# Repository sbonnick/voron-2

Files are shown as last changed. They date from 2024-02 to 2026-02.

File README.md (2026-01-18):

# voron-2

this repository contains everything you need image, update and operate a voron 2.4r2 3D printer. There are several mods used on my current voron 2.4r2 setup. These mods will be made clear if they require code or system level changes. If you do not have specific mods I will attempt to make it clear what alternative configurations are needed when possible. 

## Roadmap

This repo and doc is still missing some critical items to be fully up and running. some of these items that need to be dome before that milestone is reached are:

TODO:
- [ ] rewire octopus to use usb or CAN
- [ ] identify the configuration items that need to be adjusted
- [ ] script binary creation. use docker
- [ ] more details for the first init setup
- [ ] need to add knomi v2
- [ ] need to add chamber sensor
- [ ] consider adding a heat up (120c) and clean of nozzle before the z calibration
- [ ] create docker for katapult
- [ ] fully automate upgrading binaries

## Component Variants and Mods

| Description | Hardware Variants | Mods | Software Impacts |
| ---|---|---|---|
| Linux PCB | Pi4 2G - piOS | heat sync | Major |
| Main MCU PCB | BTT Octopus Pro | | Major |
| Toolhead PCB | BTT EBB 2240 CAN | [motor mount, cable chain arm](https://github.com/bigtreetech/EBB/tree/master/EBB%20SB2240_2209%20CAN/STL), [cable cover](https://www.printables.com/model/1216990-stealthburner-cable-cover-for-sb2209-rp2040) | Major |
| USB to CAN | BTT U2C | [mount](https://mods.vorondesign.com/detail/guUSuCXHsOqPH1Xn5cS1Ag) | Major |
| Extruder Motor | LDO-36STH20 | | |
| Z Motors | LDO-42STH48 | | Minor |
| A/B Motors | LDO-42STH40 | [plug mounts](https://github.com/Ramalama2/Voron-2-Mods/tree/main/AB_Plugs), [cable clips](https://github.com/Ramalama2/Voron-2-Mods/tree/main/Misumi_Cable_Clip) | Minor |
| Hotend | Voron Dragon HF | | |
| Extrusion support | Titanium Extrusion Backers | | |
| Kinematic Bed |  | [kinematic parts](https://github.com/tanaes/whopping_Voron_mods/tree/main/kinematic_bed) | |
| Hotend cleaning | nozzle scrubber | [brush wiper](https://www.printables.com/model/768112-voron-24-a1-bambu-silicone-brush-wiper), [brush mount](https://www.printables.com/model/659369-voron-24-purge-bucket-silicon-brush-wiper), [Purge Bucket for Kinematic](https://github.com/Dfdye/Voron_Mods/tree/main/Purge_Bucket_for_WP_Kinetic_Mount) | Minor |
| Run out sensor | BTT SFS v2.0 Sensor | [mount](https://www.printables.com/model/713155-bigtreetech-smart-filament-sensor-sfs-v20-2020-ext) | Minor |
| Exhaust | ? | ? | Minor |
| Air Filter | Nevermore 5 v2 | [parts](https://github.com/nevermore3d/Nevermore_Micro/tree/master/V5_Duo/V2) | Minor |
| X/Y End stops | Mellow Hall PCB | | Minor |
| Probe / Z end stop | CNC Voron Tap v2 | [hall sensor mount](https://github.com/Chaoticlab/CNC-Tap-for-Voron/blob/master/STL/CNC_VORON_TAP_V2/V2%20Hall%20Sensor%20Adapter.STL) | Major |
| Misc. wiring mods |  | [rails](https://mods.vorondesign.com/detail/ozerX2agbmmnjUP4EdDyQ), [under bed wagos](https://mods.vorondesign.com/detail/Zdq86RuSkhr4bx3xrauw) | |
| Misc. case mods |  | [hinges](https://mods.vorondesign.com/detail/eeRCH8EJiLrIF5q5l3AQg), [lean supports](https://mods.vorondesign.com/detail/tiIhFDTh9tHJY0JNJK9A), [handles](https://mods.vorondesign.com/detail/EAM1ZiQJCUzXznvOA767w), [magnets mount top](https://www.teamfdm.com/files/file/324-magnetic-panels/), [bottom panel tabs](https://www.teamfdm.com/files/file/134-deck-panel-support-clips/) | |
| Lights | | [mount segment](https://mods.vorondesign.com/detail/8S6KN4daUCgRhEJEX1stQ), [mount ends](https://github.com/Ramalama2/Voron-2-Mods/tree/main/Deprecated/Misumi_Led_Corners/STL), [idler corners](https://mods.vorondesign.com/detail/zBJTvWc9vSnnQoDDP0hyYw), [z corner covers](https://www.printables.com/model/84736-z-belt-cover-a-for-voron-24) | |
| power supply mods |  | [double din mount](https://www.teamfdm.com/files/file/457-double-din-lrs200-24-mounts-for-voron-24/), [terminal cover](https://mods.vorondesign.com/detail/jyO8bHoPTy3XUaYlXscB7w) | |
| Thermistor | PT100 | | Minor |
| Web Camera | Logitech C920s | [Top Mount](https://mods.vorondesign.com/detail/XgriEYTt4Xl5LeDx5DnPRg) | Major |
| Umbilical clamps | Canbus | [Clamps](https://makerworld.com/en/models/142656-voron-cable-clamp-umbilical-mod-canbus#profileId-180684) | Minor |

All mods are also stored in the stl folder for version locking. As I upgrade versions these will be upgraded as well based on the original authors revisions.

## Wiring

| Description | Images |
|---|---|
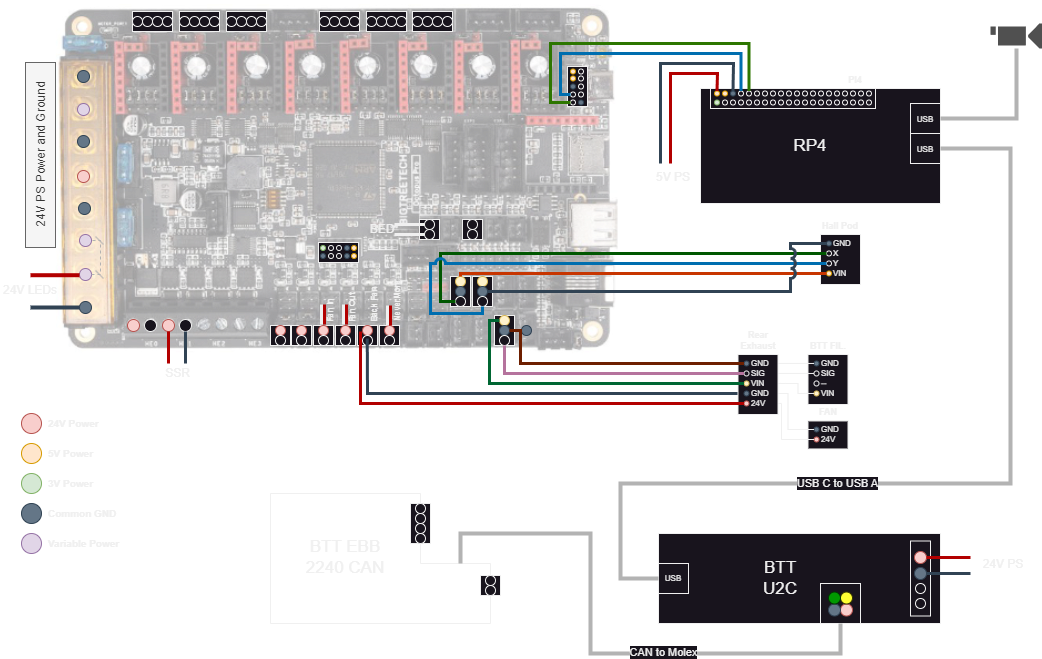
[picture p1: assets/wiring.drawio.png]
wiring diagram
| Overall wiring diagram |  |
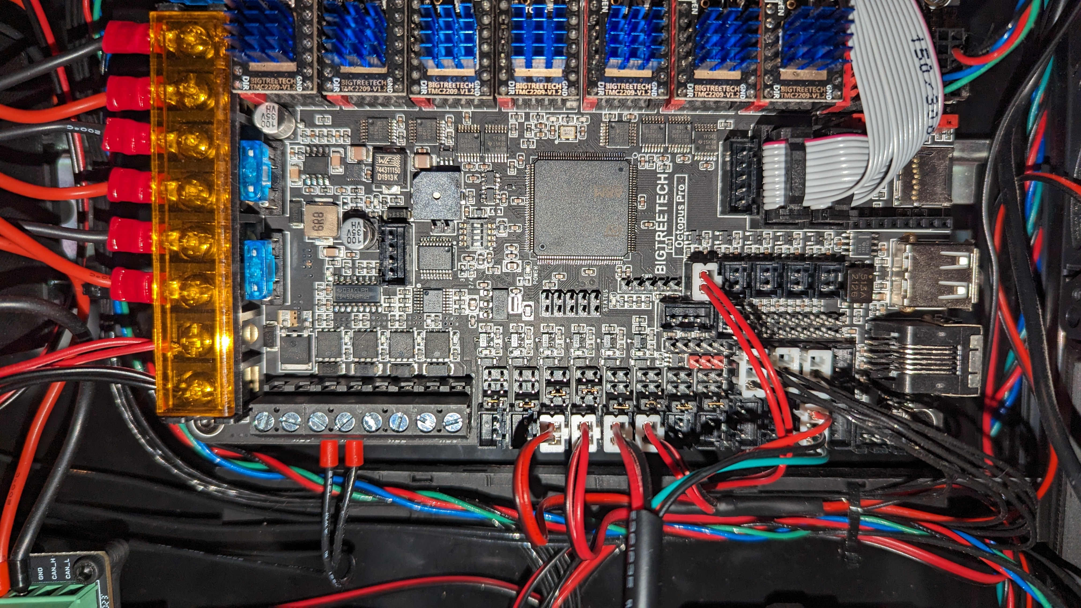
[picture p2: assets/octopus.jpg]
octopus
| Wiring for the Octopus. Note that currently the Octopus is using serial to communicate with the pi4. a future iteration I plan to switch back to usb connection or CAN |  |
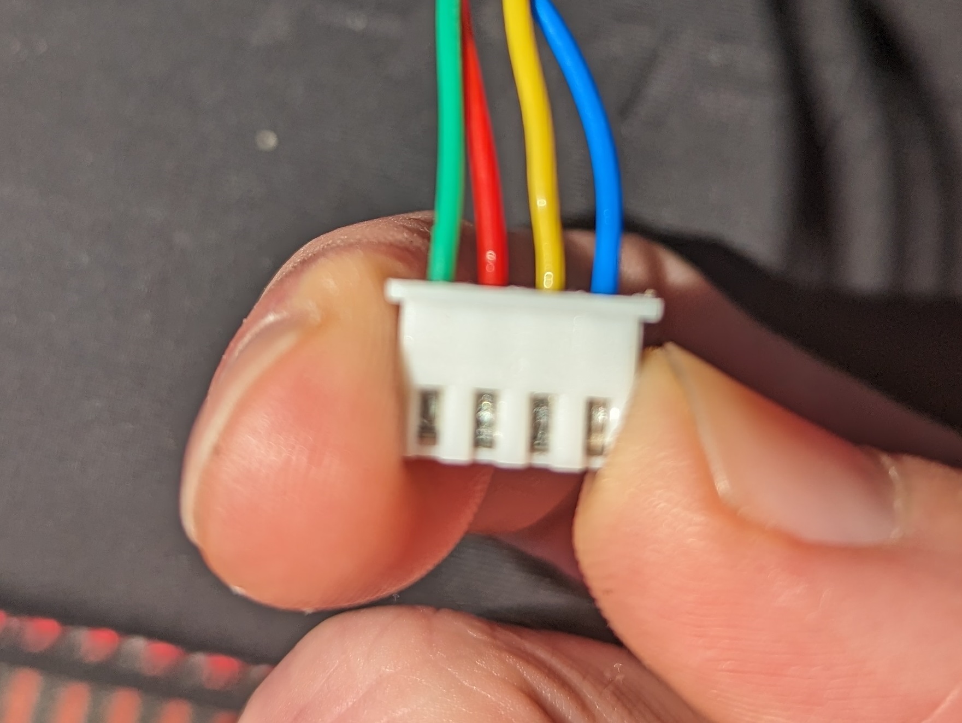
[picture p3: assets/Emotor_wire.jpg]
Extruder motor wiring
| When shortening the extruder wire, it will also require reordering the pins. Here is the order if its the LDO 20mm motor. If you use a different motor ensure you have the ordering correct |  |
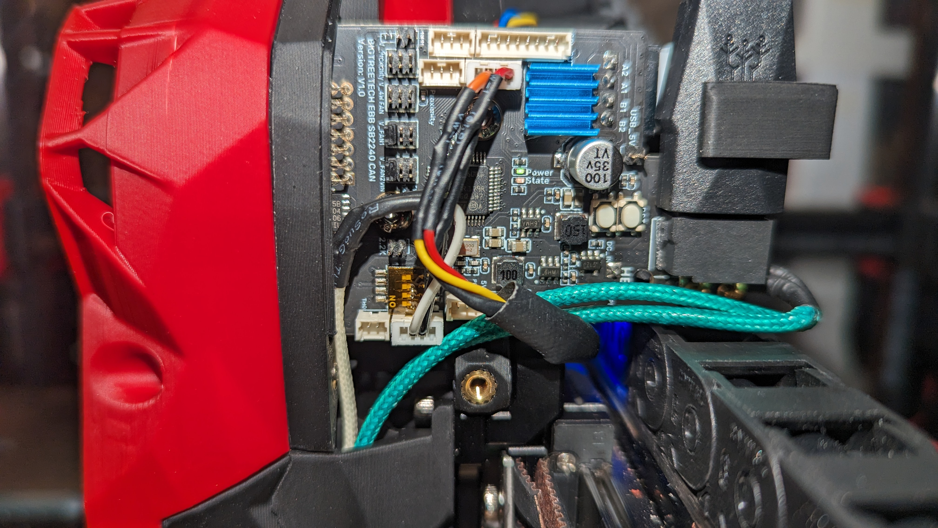
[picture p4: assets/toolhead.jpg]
Toolhead wiring
| Wiring for BTT EBB 2240 CAN Toolhead. Using PT100 (set the dip switches!) LDO motor wired above, and a voron TAP |  |
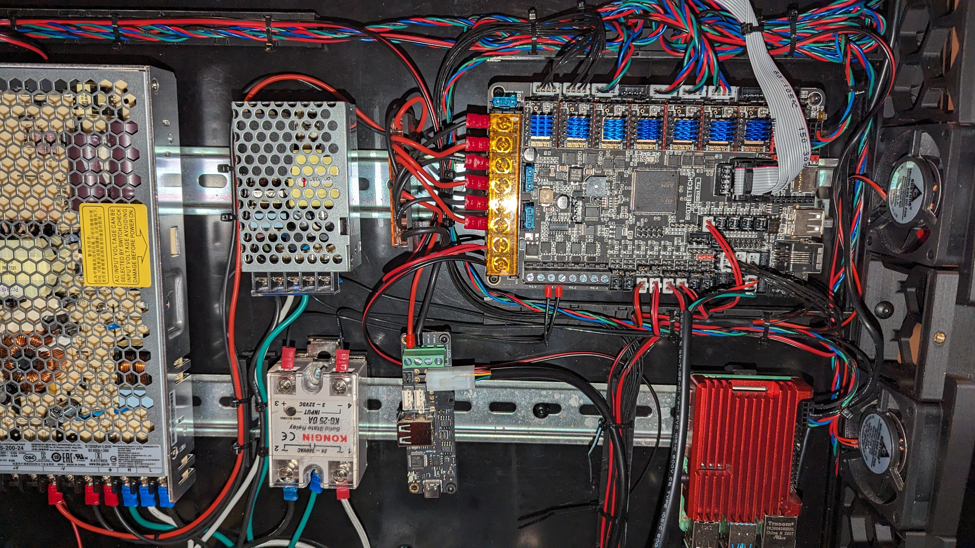
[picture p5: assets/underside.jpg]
underside
| Overall view of underside of voron 2 fully wired with all mods in place | |

## System Provisioning and Firmware

### Setup RaspberryPi 4 and Essential Software

Download the raspberry pi imaging tool and follow the steps to edit settings for an appropriate hostname, username, password, timezone, and ssh to format a micro sd card. Then install into the raspberry pi. Follow the rest of the steps over SSH.

Following SSH into the new machine, run the following:
```
sudo apt update
sudo apt upgrade -y
curl -sSL https://get.docker.com | sh
sudo usermod -aG docker $USER
sudo apt-get install gcc-arm-none-eabi dfu-util
```

### Setup UART

1. Disable bt
```
sudo nano /boot/firmware/config.txt
```
2. add the following
```
dtoverlay=disable-bt
```
3. remove `console=serial0,115200` from cmdLine.txt file
```
sudo nano /boot/firmware/cmdline.txt
```
4. reboot

### Setup U2C

1. Enter the following command to setup the CAN Network
```
sudo systemctl enable systemd-networkd
sudo systemctl start systemd-networkd
sudo systemctl disable systemd-networkd-wait-online.service
echo -e 'SUBSYSTEM=="net", ACTION=="change|add", KERNEL=="can*"  ATTR{tx_queue_len}="128"' | sudo tee /etc/udev/rules.d/10-can.rules > /dev/null
echo -e "[Match]\nName=can*\n\n[CAN]\nBitRate=1M\n\n[Link]\nRequiredForOnline=no" | sudo tee /etc/systemd/network/25-can.network > /dev/null
sudo reboot now

```
2. Install repos we know we will need to use
```
git clone https://github.com/Arksine/katapult.git
git clone https://github.com/sbonnick/voron-2.git

```
3. Setup docker stack
```
mkdir -p ~/core/klipper/log
mkdir -p ~/core/klipper/config
mkdir -p ~/core/klipper/moonraker-db
nano ~/core/.env
```
4. Add the following content to the .env
```
PUID=1000
PGID=1000
TZ="America/Toronto"
INSTALLDIR=/home/administrator/core
```
5. Copy specific files
```
cp ~/voron-2/docker-compose.* ~/core/
cp ~/voron-2/configs/klipper/* ~/core/klipper/config/
```
6. Modify docker compose file and klipper configs accordingly

### Setup Toolhead MCU

To reduce wiring complexity and portability, I have replaced my hardwired toolhead with BTTs EBB 2240 CAN board. If you are using a hard wired setup using something like a Hartk PCB, you can ignore these setup steps since your toolhead will not have a independent MCU. Caution though, your wiring will look very different as a result. refer to a older check-in here if you want to see my legacy Hartk PCB setup.

#### Building and Installing Katapult (Canboot) on EBB

1. Ensure 24V power and CAN lines are unplugged. Plug usb-c into the EBB 2240 and set the usb-c 5v power jumper
2. Run the following commands, or jump to the next step if using the prebuilt binary
```
cd katapult
make -f ../configs/toolhead.katapult.config
cd ..
```
3. Enter DFU mode on the toolhead by holding boot and clicking reset
4. Run `lsusb` and use the USB ID in the following command to flash the pre-built binary `~/voron-2/bin/toolhead.katapult.bin` or the one created in `~/katapult/out/katapult.bin`.
```
sudo dfu-util -a 0 -d 0483:df11 -s 0x08000000:mass-erase:force -D ~/CanBoot/out/canboot.bin
```
5. remove usb-c and 5v jumper. Hook back up the 24V power and CAN lines.

#### Building and Installing Klipper on EBB (fresh install or upgrade)

Before updating firmware, you need to ensure the same version of klipper is being used. Create a `.env` file and add the tag that is being used by the klipper app in docker. for example `TAG=v0.12.0-439-g1fc6d214f`. this can be retrieved using:
```
docker inspect --format '{{ index .Config.Labels "org.prind.image.version"}}' klipper
```

1. Run the following commands, or jump to the next step if using the prebuilt binary
```
cd ~/core
docker-compose -f docker-compose.toolhead.build.yml run --rm make
cp ./klipper/out/klipper.bin toolhead.klipper.bin
```
2. Run the following commands to get into katapult bootloader
```
python3 ~/katapult/scripts/flashtool.py -i can0 -r -u 8b07d889b7ef
python3 ~/katapult/scripts/flashtool.py -i can0 -q	# should show katapult app
```
If you don't already have your ID, then you need to double click the reset button (back button) on the toolhead to get into this mode. you can then run the query (-q) with same expectations. It will also provide your ID.

3. Flash the binary we create earlier
```
python3 ~/katapult/scripts/flashtool.py -i can0 -f ~/voron-2/bin/toolhead.klipper.bin -u 8b07d889b7ef
python3 ~/katapult/scripts/flashtool.py -i can0 -q	# should show klipper app
```
4. Cycle power

### Setup Octopus MCU

Before updating firmware, you need to ensure the same version of klipper is being used. Create a `.env` file and add the tag that is being used by the klipper app in docker. for example `TAG=v0.12.0-439-g1fc6d214f`. this can be retrieved using:
```
docker inspect --format '{{ index .Config.Labels "org.prind.image.version"}}' klipper
```

1. Run the following commands, or jump to the next step if using the prebuilt binary
```
cd ~/core
docker-compose -f docker-compose.octopus.build.yml run --rm make
cp ./klipper/out/klipper.bin octopus.klipper.bin
```
2. Use the samba share to copy the bin to a sd-card on your computer. rename the file `firmware.bin`.
3. Insert the sd-card into your octopus mcu and reboot (cycle power)
4. Wait 5 minutes, power down and remove sd-card. power back on
5. validate there is no longer a `firmware.bin` on the sd-card

## Klipper Configuration

TODO: list here any parameters that need to be adjusted from the `klipper.cfg` included.

## Initial Setup and Test

Once wiring and software are up and going, run through the tests and setup on:

- https://ellis3dp.com/Print-Tuning-Guide
- https://www.klipper3d.org/Config_checks.html

To calibrate dimensions of your printer use the follow pattern:

- [Calistar](https://thangs.com/designer/realdirtdigger/3d-model/Calistar%20%28formerly%20Fleur%20de%20Cali%29%20-%20Open%20source%20printer%20size%20and%20skew%20calibration-102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)

Anytime something changes that can effect the thermals of the printer, pid calibration is needed. changing sensors, hotends, etc would require this. The following command can be run in fluidd terminal and will output new pid values to be added into the printer.cfg. 
```
PID_CALIBRATE HEATER=extruder TARGET=260

or

PID_CALIBRATE HEATER=heater_bed TARGET=105
```

Anytime mechanical parts are changed, you need to redo the resonance testing:
```
SHAPER_CALIBRATE
```

## Slicing

TODO: add slicer specific settings and steps to do. OrcaSlicer configuration steps are a good one.

### Cura

Install cura from: https://ultimaker.com/software/ultimaker-cura/

If using Cura, install the following Plugins:
- Settings Guide
- Linear Advance Settings
- Mesh Tools
- Moonraker Connection
- Settings Exporter

Download the following script and install as per instructions:
- https://github.com/pedrolamas/klipper-preprocessor

Download latest processor.exe and put on C: path:
- https://github.com/kageurufu/preprocess_cancellation/releases

Setup machine called `Voron2 350`
1. X,Y,Z = 350.0
2. Build plate shape = Rectangular
3. Origin at center, Headed build volume = off
4. Heated Bed = on
5. G-code flavor = Marlin
6. Printhead: Xmin = -35, Ymin = -50, Xmax = 35, Ymax = 65, Gantry Height = 30.0, #extruders = 1, Apply offsets = on
7. Start G-code:
`print_start EXTRUDER={material_print_temperature_layer_0} BED={material_bed_temperature_layer_0} CHAMBER={build_volume_temperature}`
8. End G-code:
`print_end`
9. Nozzle settings: 1.75, 0, 0, 0, 0, 0.  No start or end codes

Setup moonraker
1. http://192.168.10.226/  (or whatever your local FIXED IP is)
2. upload: UFB with thumbnail, Upload dialog

Setup Profiles:
1. Navigate to profiles
2. import ABSplus.curaprofile and PLA.curaprofile from `slicers > cura` folder
3. when ever printing, select `Generic PLA` or `Generic ABS`, and `V6 0.40mm`. then select the corresponding profile
4. adjust support or adhesion settings as needed - should not have to change anything else

Setup Preprocessor:
1. navigate to extension > post processing scripts
2. Add klipper preprocessor script
3. print stats info = on
4. timelapse take frame = off
5. use proprocess cancellation = on
6. path = C:\preprocess_cancellation.exe
7. timeout =  600
8. klipper estimator = off

## MISC. help and references

If you run into any CAN related issues, read through the following sites: 
- https://canbus.esoterical.online
- https://github.com/Arksine/katapult

If you run into tuning related issues, read through the Ellis guide, multiple times: 
- https://ellis3dp.com/Print-Tuning-Guide

General build guides:
- https://github.com/VoronDesign/Voron-2/blob/Voron2.4/Manual/Assembly_Manual_2.4r2.pdf
- https://github.com/bigtreetech/docs/blob/master/docs/EBB%202240%202209%20CAN.md
- https://github.com/bigtreetech/docs/blob/master/docs/Octopus%20Pro.md
- https://github.com/bigtreetech/EBB/blob/master/EBB%20SB2240_2209%20CAN/Build%20Guide/EBB%20SB2240%202209%20CAN%20V1.0%20build%20guide_20240219.pdf

Much of the docker code is from the following repo with some improvements committed back to the author via issues. Strongly suggest using the docker compose files here if you don't want to use my more opinionated setup. https://github.com/mkuf/prind

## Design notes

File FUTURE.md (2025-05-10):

# Future ideas or upgrades to explore

## moving to umbilical design
https://www.printables.com/model/998448-pg7_umbilical-mount_rear_open
https://www.printables.com/model/1046156-sb2209sb2240-cw2-cable-bridge-pg7-w-cutout-for-can
https://www.printables.com/model/964357-sb2209-sb2240-cw2-cable-bridge-pg7

## 120mm exhaust
https://github.com/VoronDesign/VoronUsers/tree/main/printer_mods/hergtoler/exhaust_120mm_duct

## Thermal expansion
https://www.klipper3d.org/Config_Reference.html#z_thermal_adjust
https://github.com/alchemyEngine/measure_thermal_behavior

## Galileo 2
https://github.com/JaredC01/Galileo2
Will this allow printing faster or more reliable?
https://www.printables.com/model/711815-pivoting-bowden-guide-wzip-tie-cradle-for-canbus-w

## Plate level camera
https://github.com/3DO-EU/usb-camera/tree/main/printers/voron_v2_4

## New Purge bucket
https://www.printables.com/model/796563-voron-24-silicone-nozzle-scrubber-w-sheet-stops-be

go through following articles and see if valid:
https://all3dp.com/2/xyz-calibration-cube-troubleshooting-3d-printer/#google_vignette
https://the3dprinterbee.com/3d-printer-xyz-calibration/
https://3dprinterly.com/how-to-get-the-perfect-jerk-acceleration-setting/
https://3dprinterly.com/3d-printing-ghosting-ringing-echoing-rippling-how-to-solve/

tension calibration steps needed. this article has the frequency over 15cm
https://docs.vorondesign.com/build/mechanical/v2_gantry_squaring.html

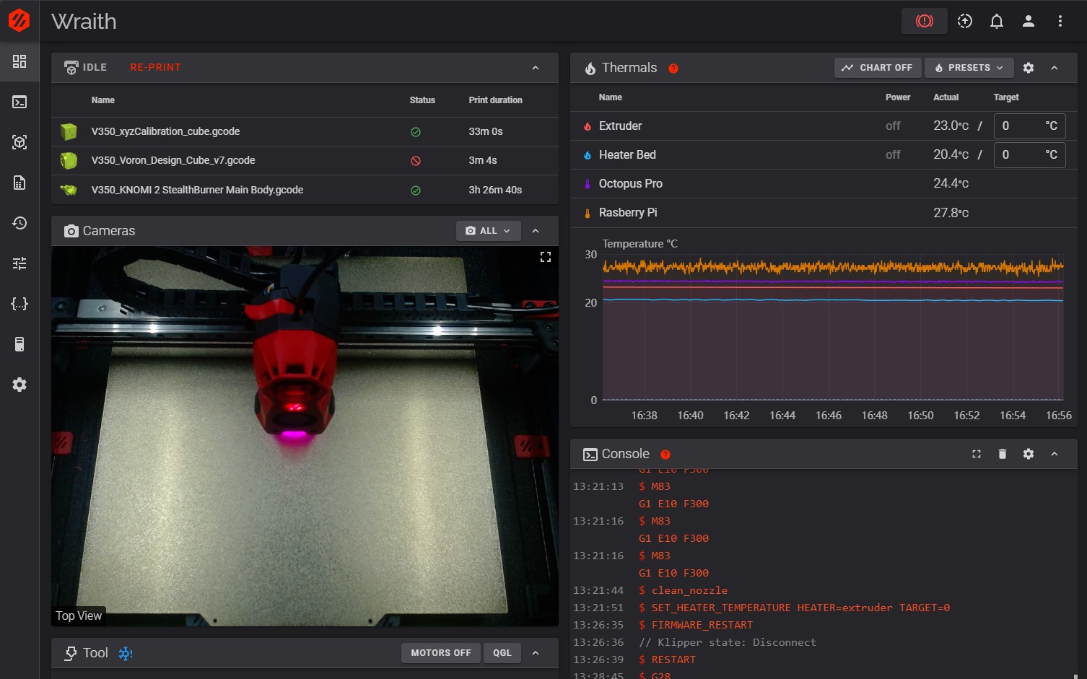
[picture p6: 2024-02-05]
assets/fluidd.jpg

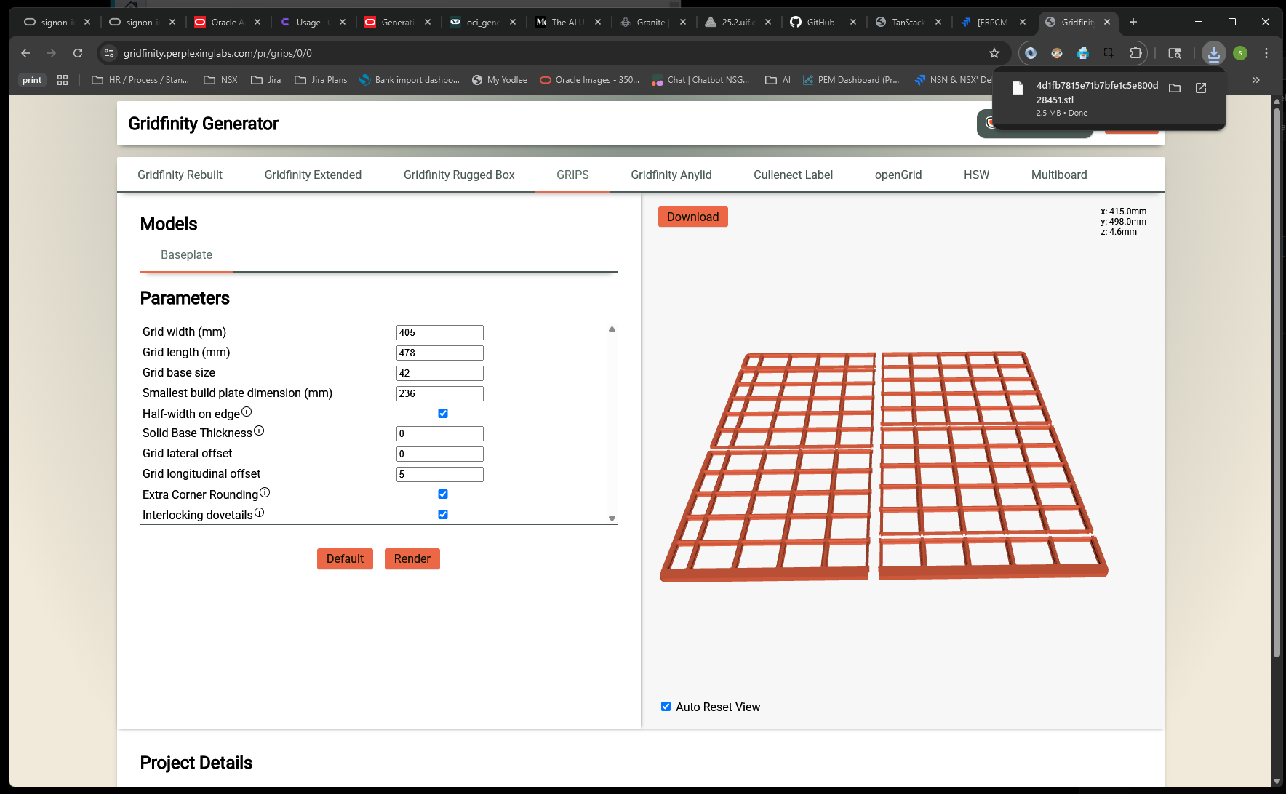
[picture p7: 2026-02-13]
stls/rack-drawers/Screenshot 2025-06-16 080830.png

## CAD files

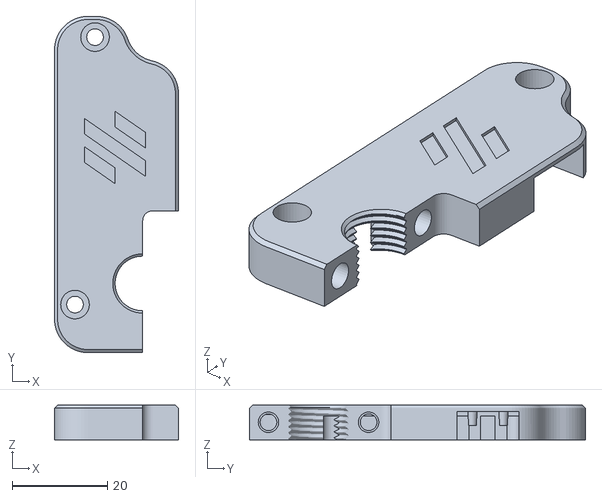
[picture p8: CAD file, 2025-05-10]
stls/PG7_umbilical-mount_rear_open v1_MAIN.stl
26.0 x 70.5 x 7.30

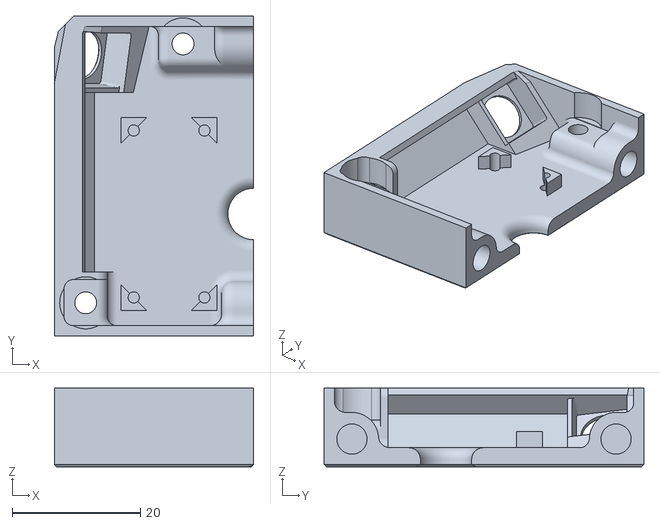
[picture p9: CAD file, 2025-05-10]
stls/3DO_USB_Camera_v2.4_corner_mount_A3_v16-Main_body.stl
31.0 x 49.8 x 12.3

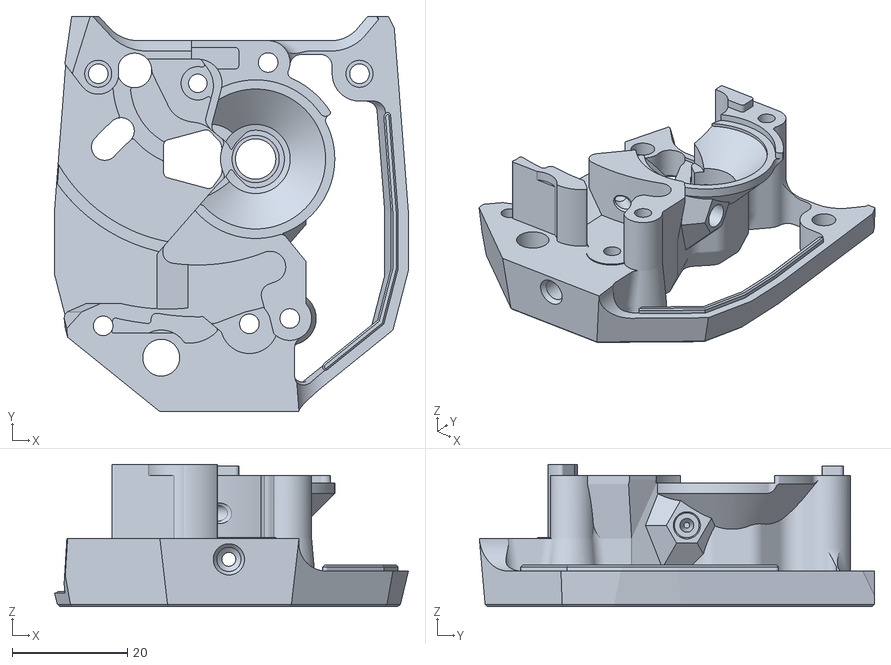
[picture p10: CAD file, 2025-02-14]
stls/Main_Body_EBB.stl
61.5 x 68.7 x 24.7

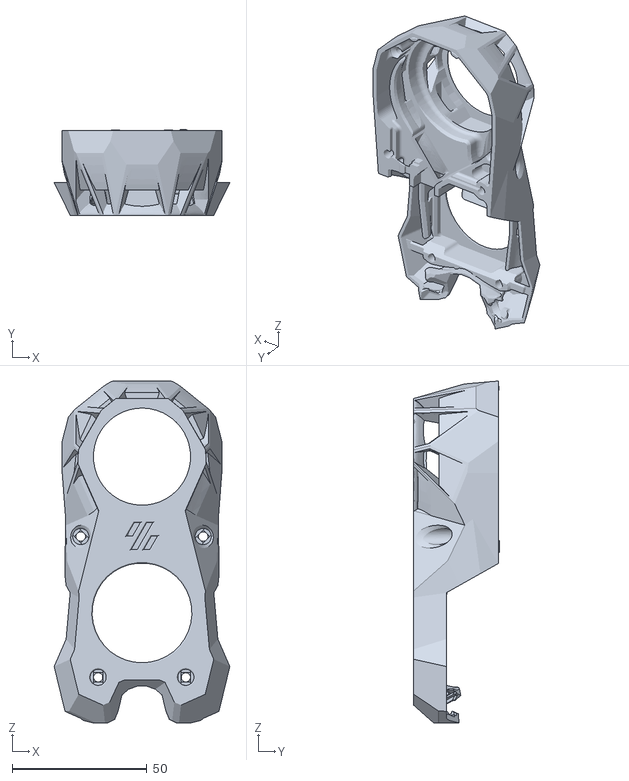
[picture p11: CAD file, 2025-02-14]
stls/KNOMI 2 StealthBurner Main Body前罩.STL
65.1 x 31.8 x 126.8

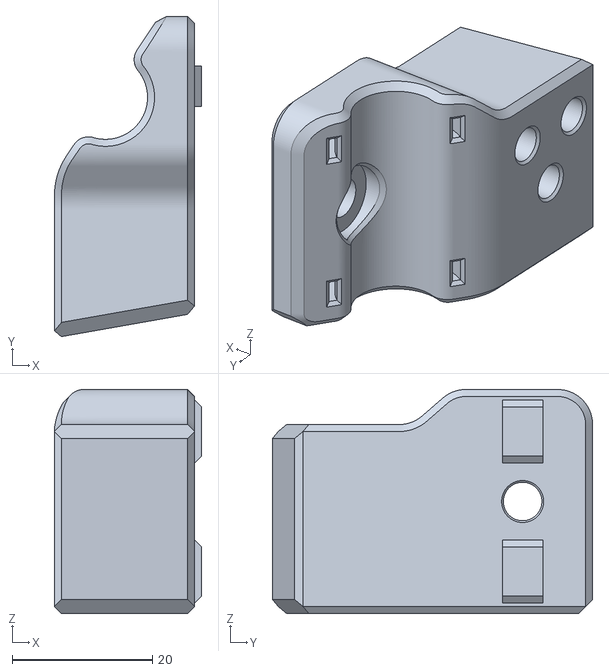
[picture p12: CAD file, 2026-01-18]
stls/Lower Mount.stl
21.0 x 45.8 x 32.0

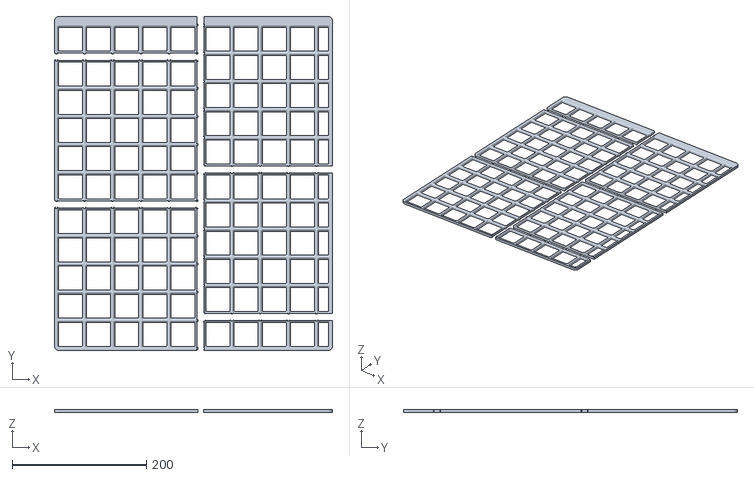
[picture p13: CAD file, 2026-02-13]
stls/rack-drawers/4d1fb7815e71b7bfe1c5e800d426f21edbd28451.stl
415.0 x 498.0 x 4.60

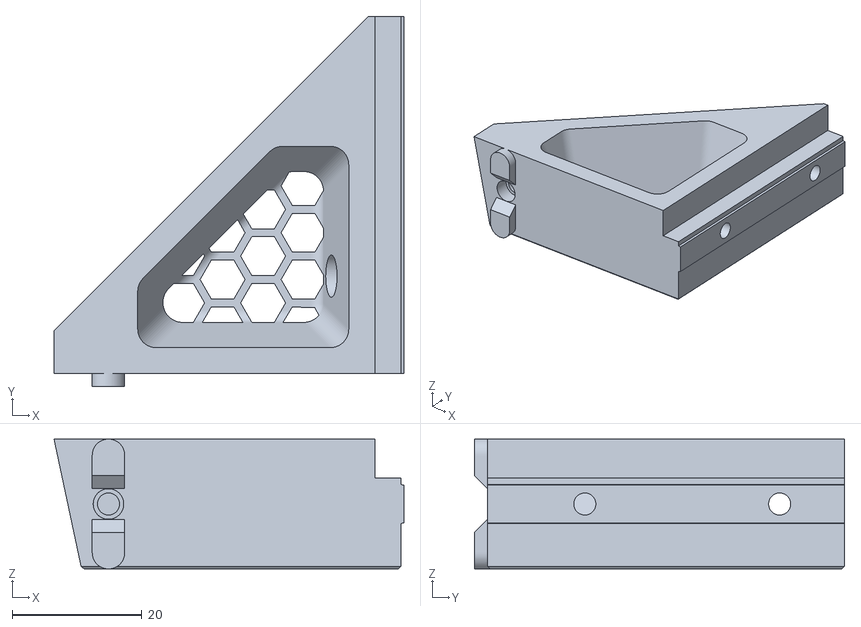
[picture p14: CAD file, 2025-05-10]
stls/Rockers/rocker_left_brace.stl
53.9 x 57.0 x 20.0

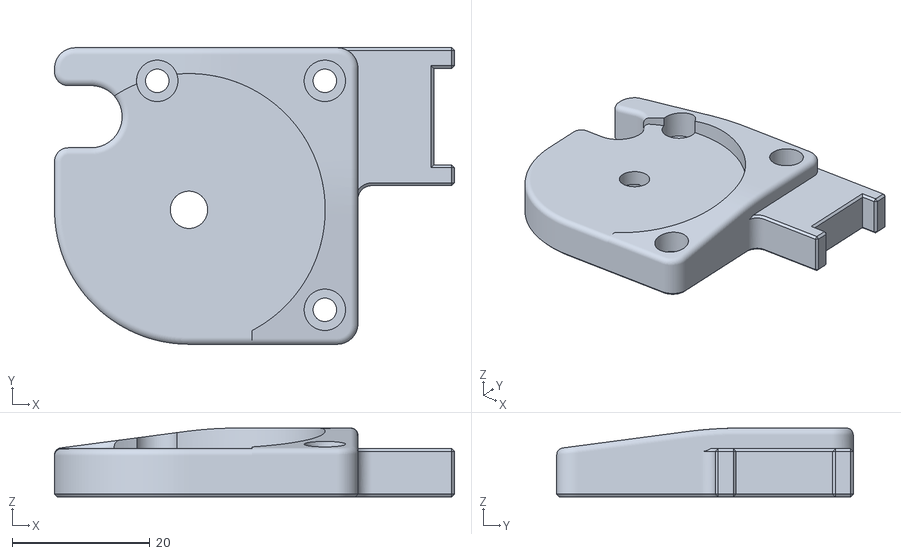
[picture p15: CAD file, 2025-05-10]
stls/Rockers/[a]_z_drive_baseplate_a_rnl_mod_r2.stl
58.0 x 43.0 x 10.0

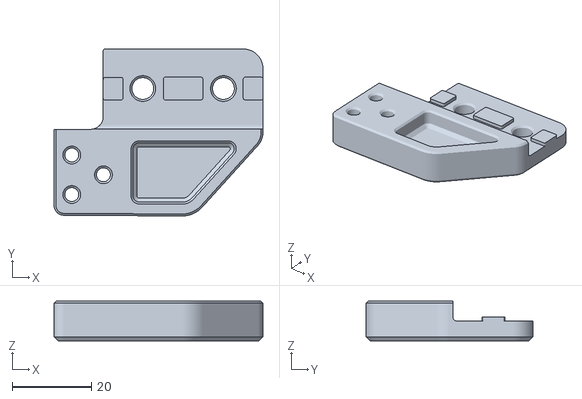
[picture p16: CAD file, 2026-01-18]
stls/Upper Mount.stl
52.9 x 42.2 x 10.00

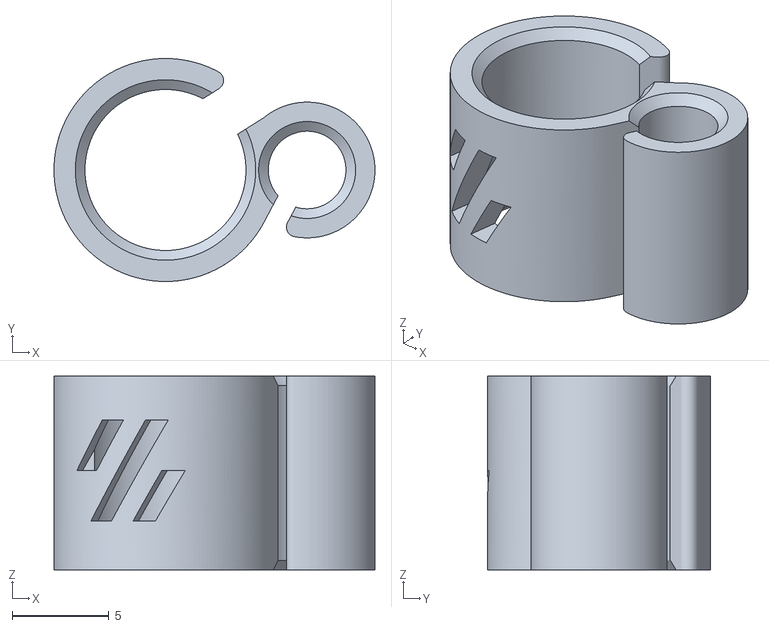
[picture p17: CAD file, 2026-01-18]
stls/8mm_clip.stl
16.6 x 11.5 x 10.0

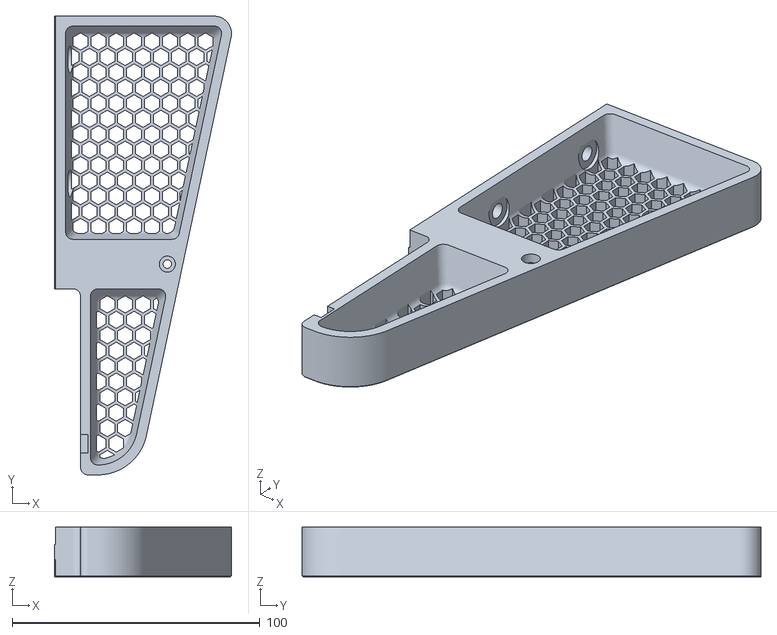
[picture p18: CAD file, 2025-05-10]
stls/Rockers/rocker_right.stl
71.4 x 185.0 x 20.0

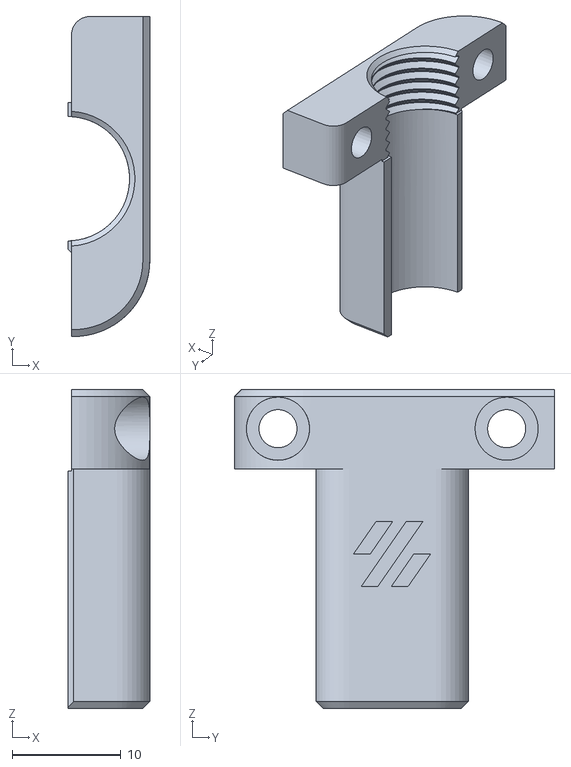
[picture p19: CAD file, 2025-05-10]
stls/PG7_umbilical-mount_rear_open_CLAMP.stl
7.50 x 29.4 x 29.3

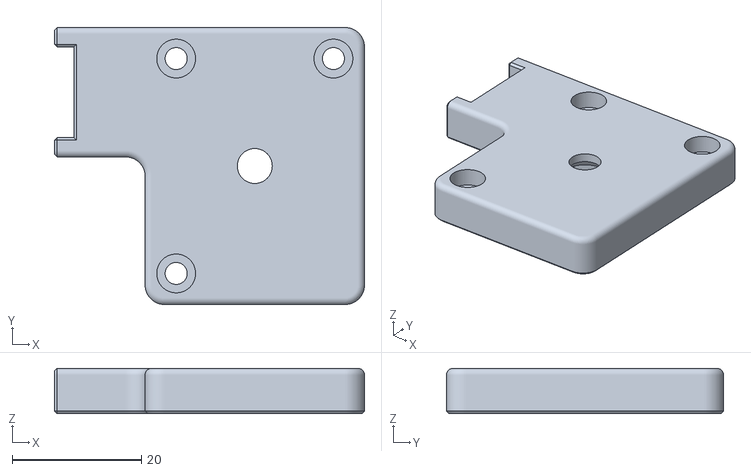
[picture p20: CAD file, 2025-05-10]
stls/Rockers/[a]_z_drive_baseplate_b_rnl_mod_r1.stl
47.9 x 42.8 x 7.00

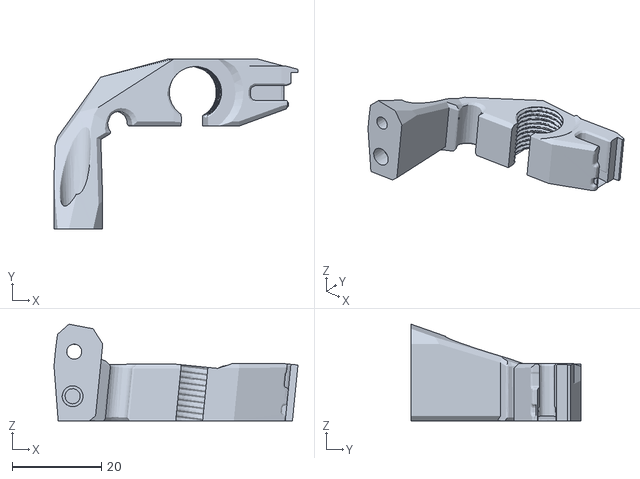
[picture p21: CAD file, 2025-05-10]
stls/CW2 Cable Bridge PG7 Cutout.stl
54.7 x 38.1 x 21.7

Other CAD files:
stls/Rockers/rocker_right_brace.stl
stls/3DO_USB_Camera_v2.4_corner_mount_A3_v16-Extrusion_mount.stl
stls/Rockers/rocker_left.stl
stls/BelterTensionTip.3mf
stls/3DO_USB_Camera_v2.4_corner_mount_A3_v16-Cover_Voron_logo.stl
stls/Bigtreetech Smart Filament Sensor V2 mount.stl
stls/CW2 Cable Bridge for EBB with cable chain.stl
stls/Cable_Cover_For_PCB_V1.2.stl
stls/KNOMI 2 Mounting Plate固定卡环.stl
stls/Rockers/[a]_z_drive_baseplate_a_rnl_mod_r1.stl
stls/Rockers/[a]_z_drive_baseplate_b_rnl_mod_r2.stl
stls/Spacer 1mm.stl
stls/V2 Hall Sensor Adapter.STL
stls/Voron Purgee Silicon wiper holder.stl
stls/VoronA1BambuNozzleWiper.stl
stls/Y-bumper.stl
stls/old/CW2 Cable Bridge for EBB with cable chain.stl
stls/old/Cable_Cover_For_PCB_V1.2.stl
stls/sb2209-rp2040-cable-cover.stl

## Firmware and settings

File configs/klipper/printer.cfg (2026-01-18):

# This file contains common pin mappings for the BigTreeTech OctoPus V1.
# To use this config, the firmware should be compiled for the STM32F446 with a "32KiB bootloader"
# Enable "extra low-level configuration options" and select the "12MHz crystal" as clock reference

# after running "make", copy the generated "klipper/out/klipper.bin" file to a
# file named "firmware.bin" on an SD card and then restart the OctoPus with that SD card.

# See docs/Config_Reference.md for a description of parameters.

## Voron Design VORON2 250/300/350mm BigTreeTech OctoPus V1 TMC2209 UART config

## *** THINGS TO CHANGE/CHECK: ***
## MCU paths							[mcu] section
## Thermistor types						[extruder] and [heater_bed] sections - See 'sensor types' list at end of file
## Z Endstop Switch location			[safe_z_home] section
## Homing end position				    [gcode_macro G32] section
## Z Endstop Switch  offset for Z0		[stepper_z] section
## Probe points							[quad_gantry_level] section
## Min & Max gantry corner positions	[quad_gantry_level] section
## PID tune								[extruder] and [heater_bed] sections
## Probe pin							[probe] section
## Fine tune E steps					[extruder] section


#####################################################################
# 	Feature enablement
#####################################################################

[respond]
default_type: echo

[virtual_sdcard]
path: /opt/printer_data/gcodes

[exclude_object]

[pause_resume]

[display_status]

[idle_timeout]
timeout: 1800

#####################################################################
# 	Basic Hardware Configuration
#####################################################################

[mcu]
serial: /dev/ttyAMA0
restart_method: command

[mcu toolhead]
canbus_uuid: 8b07d889b7ef   # PERSONALIZE: use the can uuid from setup  (6452980645e5)

[printer]
kinematics: corexy
max_velocity: 300
max_accel: 3000 			#Max 4000
max_z_velocity: 15 			#Max 15 for 12V TMC Drivers, can increase for 24V
max_z_accel: 350
square_corner_velocity: 5.0

#####################################################################
# 	X/Y Stepper Settings
#####################################################################

## X Stepper on MOTOR0(B Motor)
[stepper_x]
step_pin: PF13
dir_pin: PF12
enable_pin: !PF14
rotation_distance: 40
microsteps: 128
full_steps_per_rotation: 400  #set to 400 for 0.9 degree stepper
endstop_pin: !toolhead: PB6 # if using on octopus pro !PG6
position_min: 0
position_endstop: 350
position_max: 350
homing_speed: 75   #Max 100
homing_retract_dist: 5
homing_positive_dir: true

##	Make sure to update below for your relevant driver (2208 or 2209)
[tmc2209 stepper_x]
uart_pin: PC4
interpolate: false
run_current: 0.875 #run_current: 0.8
sense_resistor: 0.110
stealthchop_threshold: 0

## Y Stepper on MOTOR1 (A Motor)
[stepper_y]
step_pin: PG0
dir_pin: PG1
enable_pin: !PF15
rotation_distance: 40
microsteps: 128
full_steps_per_rotation: 400  #set to 400 for 0.9 degree stepper
endstop_pin: PG9 #!PG9  if using magnets
position_min: 0
position_endstop: 350
position_max: 350
homing_speed: 75  #Max 100
homing_retract_dist: 5
homing_positive_dir: true

##	Make sure to update below for your relevant driver (2208 or 2209)
[tmc2209 stepper_y]
uart_pin: PD11
interpolate: false
run_current: 0.875 #run_current: 0.8
sense_resistor: 0.110
stealthchop_threshold: 0

#####################################################################
# 	Z Stepper Settings
#####################################################################

## Z0 Stepper - Front Left on MOTOR2_1
[stepper_z]
step_pin: PF11
dir_pin: PG3
enable_pin: !PG5
rotation_distance: 40
gear_ratio: 80:16
microsteps: 128
endstop_pin: probe:z_virtual_endstop
position_max: 300
position_min: -5
homing_speed: 8
second_homing_speed: 3
homing_retract_dist: 3

##	Make sure to update below for your relevant driver (2208 or 2209)
[tmc2209 stepper_z]
uart_pin: PC6
interpolate: false
run_current: 0.8
sense_resistor: 0.110
stealthchop_threshold: 0

##	Z1 Stepper - Rear Left on MOTOR3
[stepper_z1]
step_pin: PG4
dir_pin: !PC1
enable_pin: !PA0
rotation_distance: 40
gear_ratio: 80:16
microsteps: 128

##	Make sure to update below for your relevant driver (2208 or 2209)
[tmc2209 stepper_z1]
uart_pin: PC7
interpolate: false
run_current: 0.8
sense_resistor: 0.110
stealthchop_threshold: 0

##	Z2 Stepper - Rear Right on MOTOR4
[stepper_z2]
step_pin: PF9
dir_pin: PF10
enable_pin: !PG2
rotation_distance: 40
gear_ratio: 80:16
microsteps: 128

##	Make sure to update below for your relevant driver (2208 or 2209)
[tmc2209 stepper_z2]
uart_pin: PF2
interpolate: false
run_current: 0.8
sense_resistor: 0.110
stealthchop_threshold: 0

##	Z3 Stepper - Front Right on MOTOR5
[stepper_z3]
step_pin: PC13
dir_pin: !PF0
enable_pin: !PF1
rotation_distance: 40
gear_ratio: 80:16
microsteps: 128

##	Make sure to update below for your relevant driver (2208 or 2209)
[tmc2209 stepper_z3]
uart_pin: PE4
interpolate: false
run_current: 0.8
sense_resistor: 0.110
stealthchop_threshold: 0

#####################################################################
# 	Extruder
#####################################################################

#	E0 on MOTOR6
[extruder]
step_pin: toolhead: PD0
dir_pin: toolhead: PD1
enable_pin: !toolhead: PD2
##	Update value below when you perform extruder calibration
##	If you ask for 100mm of filament, but in reality it is 98mm:
##	rotation_distance = <previous_rotation_distance> * <actual_extrude_distance> / 100
##  22.6789511 is a good starting point
rotation_distance: 22.412079
##	Update Gear Ratio depending on your Extruder Type
gear_ratio: 50:10				#  Use 50:10 for Stealthburner/Clockwork 2
microsteps: 32
full_steps_per_rotation: 200	#200 for 1.8 degree, 400 for 0.9 degree
nozzle_diameter: 0.400
filament_diameter: 1.750
heater_pin: toolhead: PB13
min_temp: 10
max_temp: 290
max_power: 1.0
min_extrude_temp: 11 #170
max_extrude_cross_section: 5
##	Try to keep pressure_advance below 1.0
pressure_advance: 0.04  # ABS+ 0.04   # PolyterraPLA 0.04
##	Default is 0.040, leave stock
pressure_advance_smooth_time: 0.040

## Revo Temp Sensor
sensor_type:ATC Semitec 104NT-4-R025H42G
sensor_pin: toolhead: PA3
control: pid
pid_Kp=27.121 
pid_Ki=2.916 
pid_Kd=63.058

## Dragon Temp Sensor
# sensor_type:MAX31865
# sensor_pin: toolhead: PA4
# spi_bus: spi1
# rtd_nominal_r: 100
# rtd_reference_r: 430
# rtd_num_of_wires: 2
# control: pid
# pid_Kp: 17.850
# pid_Ki: 0.810
# pid_Kd: 98.400


##	E0 on MOTOR6
##	Make sure to update below for your relevant driver (2208 or 2209)
[tmc2240 extruder]
cs_pin: toolhead: PA15
spi_software_sclk_pin: toolhead: PB10
spi_software_mosi_pin: toolhead: PB11
spi_software_miso_pin: toolhead: PB2
driver_TPFD: 0
run_current: 0.650 #0.670
interpolate: false
stealthchop_threshold: 0

#####################################################################
#   Enclosure Temp Sensor
#####################################################################

[temperature_sensor rasberry_pi]
sensor_type: temperature_host
min_temp: 0
max_temp: 90

[temperature_sensor octopus_pro]
sensor_type: temperature_mcu
min_temp: 0
max_temp: 80

[temperature_sensor toolhead]
sensor_type: Generic 3950
sensor_pin: toolhead: PA2

#####################################################################
# 	Fan Control
#####################################################################

[fan]
pin: toolhead: PA1
kick_start_time: 0.5
off_below: 0.10

[heater_fan hotend_fan]
pin: toolhead: PA0
max_power: 1.0
kick_start_time: 0.5
heater: extruder
heater_temp: 50.0

[heater_fan controllers]
pin: PD12
kick_start_time: 0.3
heater: heater_bed, extruder
heater_temp: 20.0
shutdown_speed: 0.0
fan_speed: 0.5 #0.2

[heater_fan power_supply]
pin: PD13
kick_start_time: 0.3
heater: heater_bed, extruder
heater_temp: 20.0
shutdown_speed: 0.0
fan_speed: 0.5 #0.2

[heater_fan exhaust_fan]
##	Exhaust fan - CNC_FAN4
Pin: PD14
heater: heater_bed
Heater_temp: 20.0
Shutdown_speed: 0.0
fan_speed: 0.6 #1.0

[heater_fan nevermore_fan]
pin: PD15
heater: heater_bed
heater_temp: 65.0
shutdown_speed: 0.0


#####################################################################
# 	LED Control
#####################################################################

[output_pin caselight]
# Chamber Lighting - HE2 Connector (Optional)
pin: PA1
#pwm: true
pwm: false
shutdown_value: 0
value: 1
#value: 0.5
#cycle_time: 0.001

#####################################################################
# 	Bed Heater
#####################################################################

[heater_bed]
heater_pin: PA3
sensor_type: Generic 3950
sensor_pin: PF3
max_power: 0.7 #0.6
min_temp: 0
max_temp: 120
control: pid   #calibrated to 110
pid_Kp: 36.794
pid_Ki: 1.018
pid_Kd: 332.527

#####################################################################
# 	Probe
#####################################################################
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

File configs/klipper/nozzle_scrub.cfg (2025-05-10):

#######################################################################################################################################

# Sample macro config to be used in conjunction with the Decontaminator Purge Bucket & Nozzle Scrubber mod. Created by Hernsl 
# (hernsl#8860 on Discord) and edited by Edwardyeeks (edwardyeeks#6042 on Discord). Several ideas that made it as features by
# Deutherius (deutherius#3295 on Discord).

# The goal of this macro is to provide a nozzle scrubbing and purging routine that is easily copied/referenced into your  printer.cfg.
# Users can simply change parameters and enable/disable options in the first half. Descriptions are plentiful, making this macro
# look huge but informative and are laid out in sequence to be read first describing the line below; PLEASE READ CAREFULLY.

# This sample config assumes the following: The user has implemented the default decontaminator purge bucket & nozzle scrubber mod
# for the VORON 1/2. It can be tweaked to customised purge bucket geometries and brushes.

# Features in this macro: option of putting the bucket at the rear or front of the bed. Purge routine that can be enabled/disabled.
# By default, bucket is located at rear left of bed and purge routine is enabled. The purge and scrubbing routine is randomized
# in either left or right bucket to ensure as even as possible distribution of filament gunk.

# Default parameters are set for safe speeds and movements. Where necessary, tweak the parameters for the nozzle scrub procedure 
# to fit your printer.

# To avoid adding length of lines to your main printer.cfg config file, one can upload a config file separately into klipper and
# include it into the main printer config. Upload nozzle_scrub.cfg to the same directory as printer.cfg. Usually, it is in /home/pi/.
# Users of Fluidd, Mainsail and other klipper front ends would find it under /home/pi/klipper_config/.

# Once uploaded, add the following to your printer.cfg in the Macros section: [include /home/pi/nozzle_scrub.cfg] 
# Those running Fluidd, Mainsail and other front ends will need to use the following location instead:
# [include /home/pi/klipper_config/nozzle_scrub.cfg]

#######################################################################################################################################

# Name of the macro is clean_nozzle.

[gcode_macro clean_nozzle]

# If you are putting your purge bucket at the rear left of the bed as per default installation, enable True on your location_bucket_rear 
# variable. If you want to put your purge bucket elsewhere (perhaps the front), then set it to False. See diagrams and description 
# further below on how to set your XY position.
variable_location_bucket_rear:      True

# If you want the purging routine in your bucket enabled, set to True (and vice versa).
variable_enable_purge:              False

# These parameters define your filament purging. The retract variable is used to retract right after purging to prevent unnecessary
# oozing. Some filament are particularly oozy and may continue to ooze out of the nozzle for a second or two after retracting. The
# ooze dwell variable makes allowance for this. Update as necessary. If you decided to not enable purge, you can ignore this section.
variable_purge_len:             5	         ; Amount of filament, in mm, to purge.
variable_purge_spd:           150	         ; Speed, in mm/min, of the purge.
variable_purge_temp_min:      220	         ; Minimum nozzle temperature to permit a purge. Otherwise, purge will not occur.
variable_purge_ret:             2            ; Retract length, in mm, after purging to prevent slight oozing. Adjust as necessary.
variable_ooze_dwell:            2            ; Dwell/wait time, in seconds, after purging and retracting.

# Adjust this so that your nozzle scrubs within the brush. Currently defaulted to be a lot higher for safety. Be careful not to go too low!
variable_brush_top:             3.7

# These parameters define your scrubbing, travel speeds, safe z clearance and how many times you want to wipe. Update as necessary. Wipe 
# direction is randomized based off whether the left or right bucket is randomly selected in the purge & scrubbing routine.
variable_clearance_z:           5	         ; When traveling, but not cleaning, the clearance along the z-axis between nozzle and brush.
variable_wipe_qty:              3	         ; Number of complete (A complete wipe: left, right, left OR right, left, right) wipes.
variable_prep_spd_xy:        10000	         ; Travel (not cleaning) speed along x and y-axis in mm/min.
variable_prep_spd_z:         1200	         ; Travel (not cleaning) speed along z axis in mm/min.
variable_wipe_spd_xy:        9000	         ; Nozzle wipe speed in mm/min.


# These parameters define the size of the brush. Update as necessary. A visual reference is provided below. Note that orientation of 
# parameters remain the same whether bucket is at rear or front.
# 
#                  ←   brush_width   →                            
#                   _________________                                                          ↑
#                  |                 |  ↑                     If you chose location_bucket_rear = True, Y position is acquired
#  brush_start (x) |                 | brush_depth            from your stepper_y position_max. Adjust your brush physically in
#                  |_________________|  ↓                               Y so that the nozzle scrubs within the brush.       
#                          (y)                                                                 ↓
#                      brush_front
# __________________________________________________________
#                     PRINTER FRONT
# 
# 
## For V1.8, you may need to measure where your brush is on the x axis and input manually into any of the variable_brush_start uncommented.
## For V2.4 250mm build, uncomment this below: 
#variable_brush_start:     25	    

## For V2.4 300mm build, uncomment this below:
#variable_brush_start:     50

## For V2.4 350mm build, uncomment this below:
variable_brush_start:     75

# This value is defaulted from brush location in CAD (rear left). Change if your brush width is different.
variable_brush_width:          52	

## These are only used if location_bucket_rear is False. You specify a custom location in y axis for your brush - see diagram above. ##
variable_brush_front:       0          
variable_brush_depth:       0          


# These parameters define the size of your purge bucket. Update as necessary. If you decided to not enable purge, you can ignore 
# this section. A visual reference is provided below. Note that orientation of parameters remain the same whether bucket is at rear 
# or front.
# 
#                                     bucket_gap
#                                      ← ---- →
#                     __________________________________________
#                    |                 |      |                 |      
#                    |                 |      |                 |
#  bucket_start (x)  |                 |______|                 |
#                    |                 |      |                 |
#                    |                 |      |                 |
#                    |_________________|. . . |_________________|
#                     ← ------------- →        ← ------------- →
#                     bucket_left_width        bucket_right_width
#  _______________________________________________________________________________________
#                                    PRINTER FRONT
# 
## For V2.4 250mm build, uncomment below 
variable_bucket_left_width:    42

## For V2.4 300mm build, uncomment below
#variable_bucket_left_width:    67

## For V2.4 350mm build, uncomment below
#variable_bucket_left_width:    92   

# These values are defaulted from bucket geometry in CAD (rear left location). Change only if you're using a custom bucket.
variable_bucket_right_width:   40            
variable_bucket_gap:           22	

# For V1.8, you may need to measure where your bucket start is and input into bucket_start. Otherwise, a value of 0 is for a default
# installation of purge bucket at rear left.
variable_bucket_start: 50

# If set to False will park the head to the left of the bucket when complete, otherwise will park to the right.
# This can be useful if you have a probe dock in the standard left area and you want to avoid this by parking to the left
variable_park_right: False

# By default, the move order is Z, Y, X. However this can cause a problem if you clean the head while there is a part on the build plate.
# for example after a failing print, while the hotend is still warm. To avoid any collisions, move the Y axis first such that the order
# is Y, Z, X.
variable_move_y_first: False
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

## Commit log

2024-01-23 Added pre-CAN configs
    [filament-sensor.cfg, fluidd.cfg, klicky-bed-mesh-calibrate.cfg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]
2024-01-29 Partial notes on upgrade to EBB CAN - software portion
    [klicky-bed-mesh-calibrate.cfg, klicky-macros.cfg, klicky-probe.cfg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]
2024-02-04 Added wiring images and started converting configs to support CAN head
    [filament-sensor.cfg, fluidd.cfg, nozzle_scrub.cfg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]
2024-02-05 updated wiring to include U2C and EBB
2024-02-07 simplified print_start by refactoring into sub macros
    [printer.cfg]
2024-02-08 misc updates and fixes after running on the printer
    [printer.cfg]
2024-02-11 added some more stl links
2024-02-12 added remaining STL links
2024-08-29 minor updates
    [Bigtreetech Smart Filament Sensor V2 mount.stl, CW2 Cable Bridge for EBB with cable chain.stl, Cable_Cover_For_PCB_V1.2.stl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]
2025-02-14 Added extruder tuning link
2025-02-18 improved docs around flashing binaries
    [filament-sensor.cfg, nozzle_scrub.cfg, printer.cfg]
2025-03-14 updated STLs and minor docs
    [Main_Body_EBB.stl, Spacer 1mm.stl, Voron Purgee Silicon wiper holder.stl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]
2025-05-10 Misc. Improvements
    [3DO_USB_Camera_v2.4_corner_mount_A3_v16-Cover_Voron_logo.stl, 3DO_USB_Camera_v2.4_corner_mount_A3_v16-Extrusion_mount.stl, 3DO_USB_Camera_v2.4_corner_mount_A3_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]
2026-01-18 Updated as a merge from both voron printers owned
    [8mm_clip.stl, Lower Mount.stl, Upper Mount.stl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]
2026-02-13 update stl
    [4d1fb7815e71b7bfe1c5e800d426f21edbd28451.stl]
